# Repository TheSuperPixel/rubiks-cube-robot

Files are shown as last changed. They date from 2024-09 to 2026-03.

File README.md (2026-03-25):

# 三阶魔方还原机器人
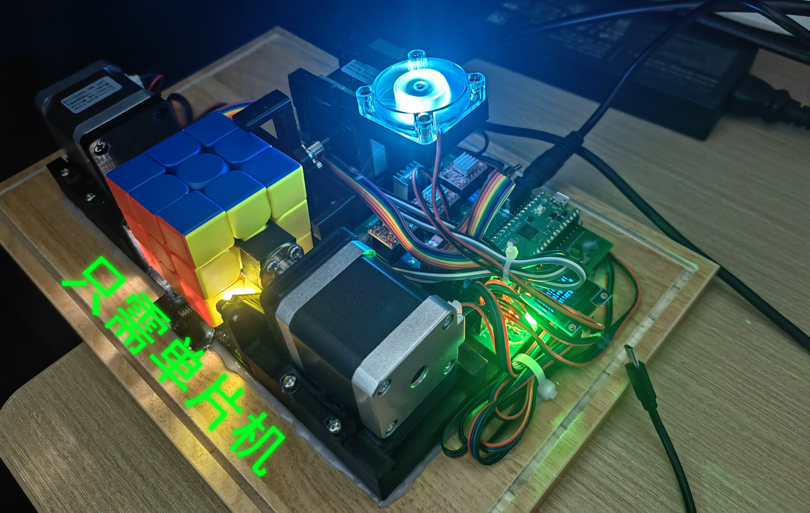
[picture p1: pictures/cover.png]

## 介绍
低成本魔方机器人设计，总物料成本200元左右。 含单片机源码（c语言）、结构图和PCB工程。 使用**树莓派pico单片机**控制，控制和魔方求解都使用单片机完成。 
工程的主要部分参照了B站“爱跑步的小何”的三阶魔方机器人开源工程，但是在这个工程的基础上，添加了江协科技的OLED驱动库，制作了用户菜单页面，使得机器人不仅能还原魔方，还能根据用户的选择，做出不同的魔方花样。
代码结构图是我在阅读原版开源项目时为了方便理解绘制的，仅供参考
## 关于硬件设计
使用嘉立创专业版打开pcb文件夹下的工程文件即可。主控选用树莓派pcio单片机，步进电机驱动模块接口连接A4988模块模块，其他元件参照电路板工程设计，焊接完成后，参照演示视频，设置拨码开关，三个电机的细分调节档位全部拨到1，颜色传感器灯开关全部拨到0，电机待机开关全部设置为无效。因为没有高速时序要求，PCB使用了自动布线，暂时不影响正常使用。

## 关于结构设计
使用**ABS材料**3D打印，尤其是夹魔方的结构件，对强度要求较高。

## 单片机固件编译(./src)
推荐使用**Linux**系统进行开发，可按照官方文档中的脚本搭建开发环境。不推荐Windows系统下搭建，坑很多的。

搭建好之后，修改**CMakeLists.txt**，把**PICO_SDK_PATH**设置为正确的路径
````
set(PICO_SDK_PATH "/home/your_name/pico2/pico-sdk")
#"your_name"need to change to your user name!
````
然后编译项目
````
cd src
mkdir build
cmake .
make -j2
````
然后找到cube_robot.uf2，刷写到单片机即可。

可以连接USB，使用minicom -D /dev/ttyACM0指令查看调试信息，例如：
````
color_detect: FLDFUUUDBDLRURRFDLBFRDFBFLRDDURDBBUBLURBLRLBLFFUFBLDRU
stage=0, D' B U' L F' 
stage=1, B2 R2 U2 F2 D R' L' U L' 
stage=2, R2 D' F2 D2 R2 D R2 D' B2 D' 
stage=3, B2 R2 U2 B2 U2 L2 U2 L2 F2 R2 B2 
````
## 参考资料
1.B站“爱跑步的小何”三阶魔方机器人工程 https://gitee.com/hemn1990/rubiks-cube-robot<br>
2.江协科技OLED驱动 https://www.bilibili.com/video/BV1EN41177Pc

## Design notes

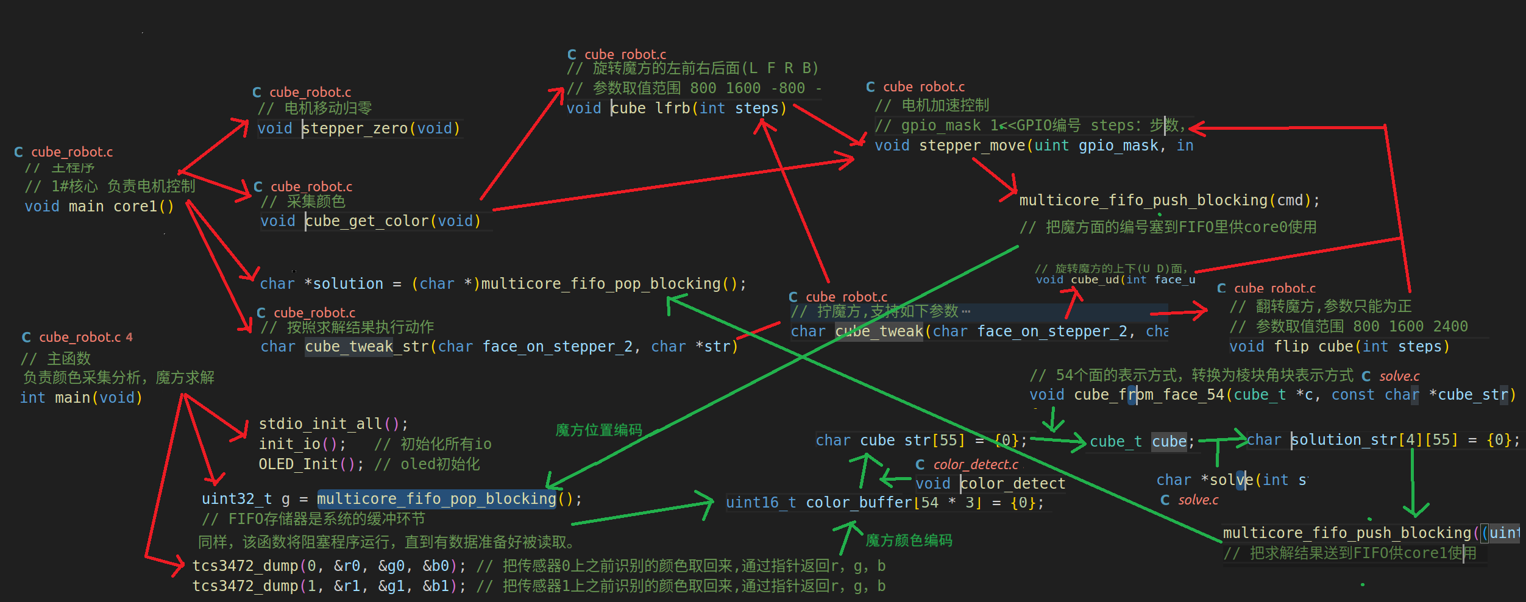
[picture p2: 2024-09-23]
代码结构.png

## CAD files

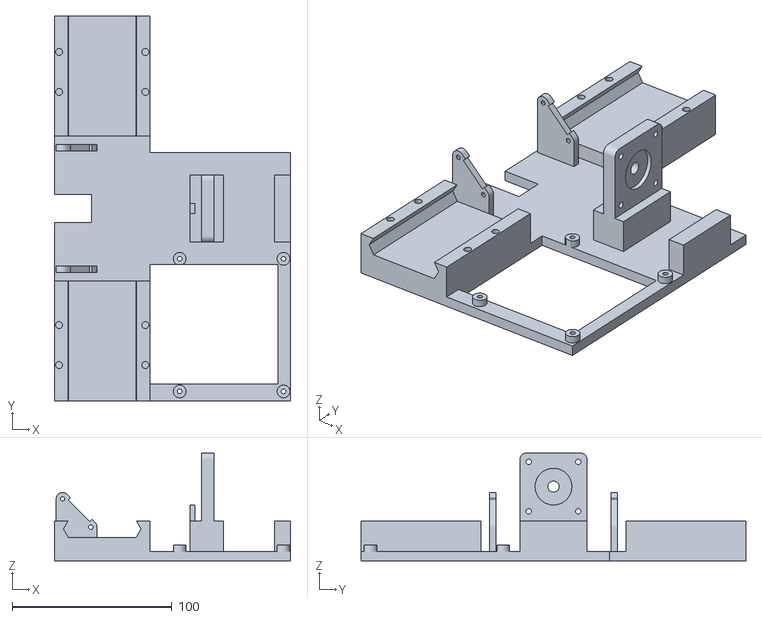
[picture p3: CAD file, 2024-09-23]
3D_print_STL/3d_print_main.stl
148.0 x 241.0 x 67.5

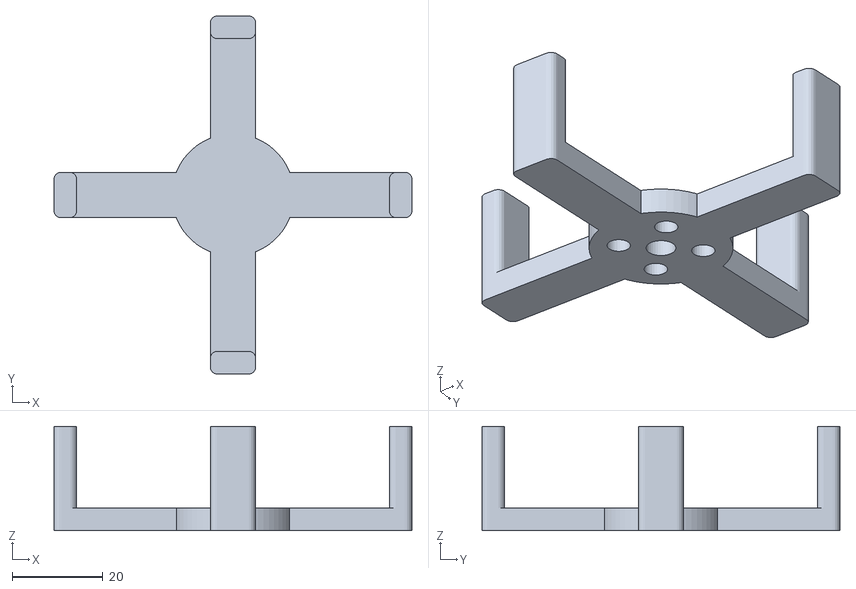
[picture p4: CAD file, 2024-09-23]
3D_print_STL/3d_print_cube_spin.stl
79.0 x 79.0 x 23.0

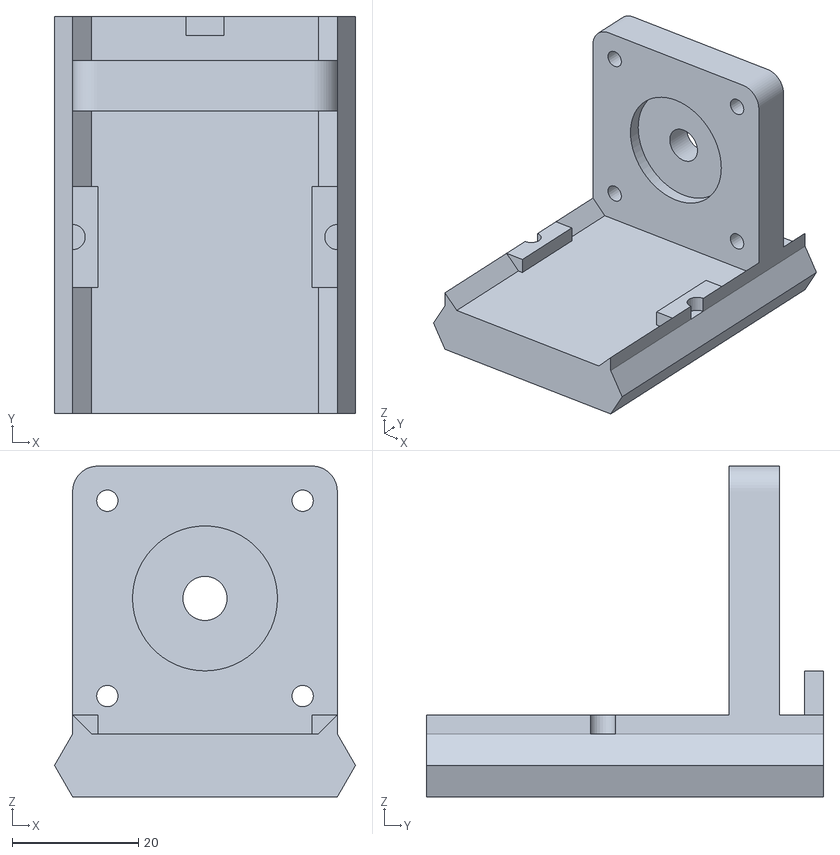
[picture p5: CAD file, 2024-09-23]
3D_print_STL/3d_print_stepper_shelf_x2.stl
47.8 x 63.0 x 52.5

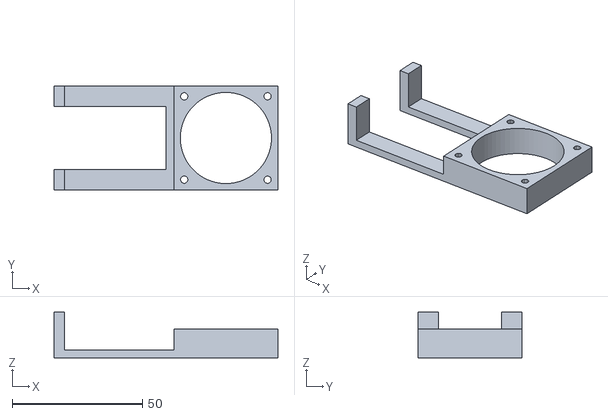
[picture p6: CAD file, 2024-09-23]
3D_print_STL/fan_holder.stl
86.0 x 40.0 x 17.5

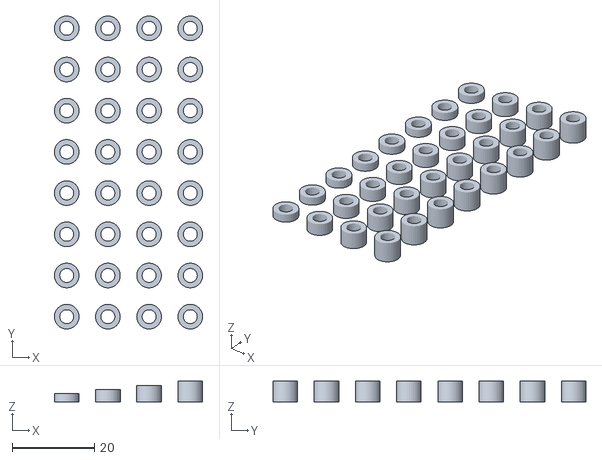
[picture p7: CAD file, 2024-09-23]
3D_print_STL/cylinder_reserve.stl
36.0 x 76.0 x 5.00

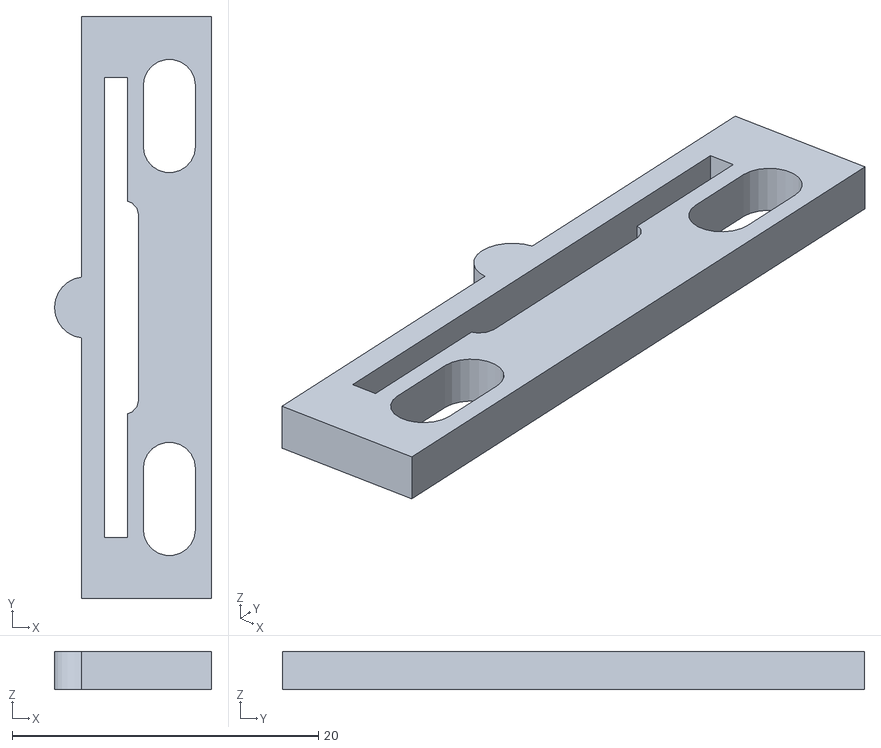
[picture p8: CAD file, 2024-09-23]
3D_print_STL/3d_print_spring_x4.stl
10.2 x 38.0 x 2.50

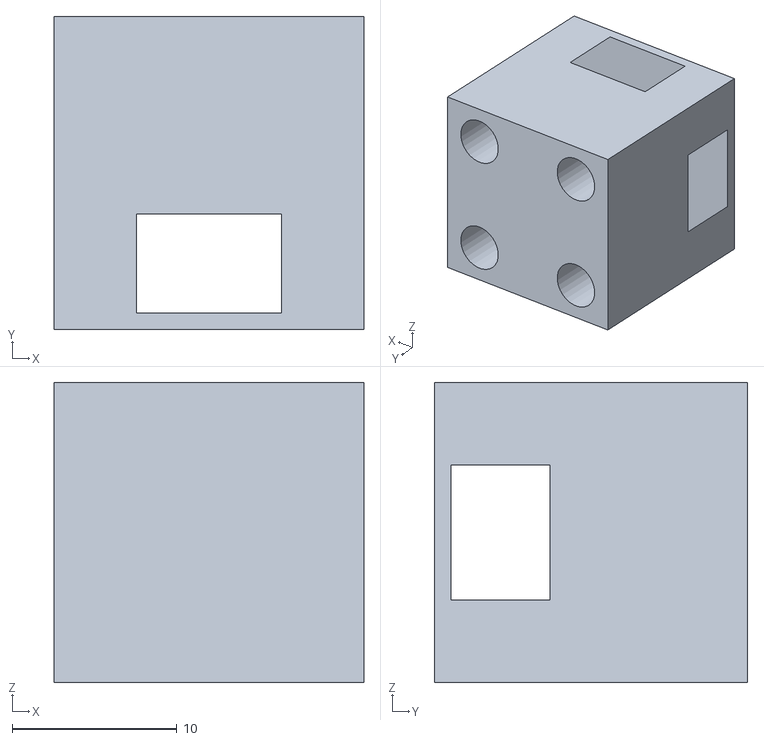
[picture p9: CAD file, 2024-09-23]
3D_print_STL/3d_print_claw_x2.stl
18.8 x 19.0 x 18.2

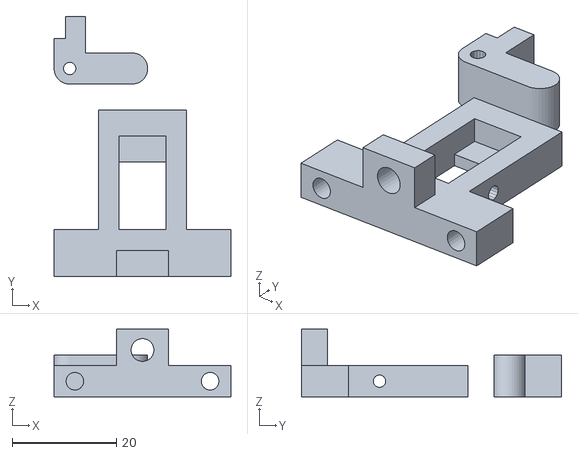
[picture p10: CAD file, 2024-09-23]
3D_print_STL/弹簧组件.stl
34.0 x 50.0 x 13.0

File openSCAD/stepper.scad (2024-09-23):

$fa=6;
$fs=0.5;



stepper42();
translate([0,0,23]) rotate([180,0,0]) flange();
module flange(){
    difference(){
        union(){
            cylinder(h=2,d=22);
            cylinder(h=12,d=10);
        }
        cylinder(h=99,d=5,center=true);
        translate([8,0,0]) cylinder(h=99,d=3,center=true);
        translate([-8,0,0]) cylinder(h=99,d=3,center=true);
        translate([0,-8,0]) cylinder(h=99,d=3,center=true);
        translate([0,8,0]) cylinder(h=99,d=3,center=true);
    }
}


module stepper42(){
    union(){
        top();
        translate([0,0,-8]) mid();
        translate([0,0,-8-9.5-23-8]) mirror([0,0,1]) bot();
    }
}


module mid(){
    mid_r = 8;
    offset_xy = 42/2 - mid_r;
    length = 23+8; // 硅钢片高度
    hull(){
        translate([offset_xy, offset_xy, -length]) cylinder(h=length, r=mid_r, $fn=4);
        translate([offset_xy, -offset_xy, -length]) cylinder(h=length, r=mid_r, $fn=4);
        translate([-offset_xy, offset_xy, -length]) cylinder(h=length, r=mid_r, $fn=4);
        translate([-offset_xy, -offset_xy, -length]) cylinder(h=length, r=mid_r, $fn=4);
    }
}
module top(){
    top_r = 4;
    offset_xy = 42/2 - top_r;
    length = 23+2; // 电机轴长度
    union(){
        difference(){
            hull(){
                translate([offset_xy, offset_xy, -8]) cylinder(h=8, r=top_r, $fn=4);
                translate([offset_xy, -offset_xy, -8]) cylinder(h=8, r=top_r, $fn=4);
                translate([-offset_xy, offset_xy, -8]) cylinder(h=8, r=top_r, $fn=4);
                translate([-offset_xy, -offset_xy, -8]) cylinder(h=8, r=top_r, $fn=4);
            }
            translate([31/2, 31/2, 0]) cylinder(h=20,d=2.5,center=true); 
            translate([-31/2, 31/2, 0]) cylinder(h=20,d=2.5,center=true);
            translate([31/2, -31/2, 0]) cylinder(h=20,d=2.5,center=true);
            translate([-31/2, -31/2, 0]) cylinder(h=20,d=2.5,center=true);       
        }
        difference(){
            cylinder(h=2,d=22);
            cylinder(h=20,d=9,center=true);
        }
        difference(){
             cylinder(h=length,d=5);
             translate([-5/2, 4.5/2, 0]) cube([5,5,length]);
        }
    }
}
module bot()
{
    bot_r = 4;
    offset_xy = 42/2 - bot_r;
    union(){
        difference(){
            hull(){
                translate([offset_xy, offset_xy, -9.5]) cylinder(h=9.5, r=bot_r, $fn=4);
                translate([offset_xy, -offset_xy, -9.5]) cylinder(h=9.5, r=bot_r, $fn=4);
                translate([-offset_xy, offset_xy, -9.5]) cylinder(h=9.5, r=bot_r, $fn=4);
                translate([-offset_xy, -offset_xy, -9.5]) cylinder(h=9.5, r=bot_r, $fn=4);
            }
            translate([31/2, 31/2, 0]) cylinder(h=20,d=3.5,center=true); 
            translate([-31/2, 31/2, 0]) cylinder(h=20,d=3.5,center=true);
            translate([31/2, -31/2, 0]) cylinder(h=20,d=3.5,center=true);
            translate([-31/2, -31/2, 0]) cylinder(h=20,d=3.5,center=true);
            translate([31/2, 31/2, -2.5]) cylinder(h=20,d=6); 
            translate([-31/2, 31/2, -2.5]) cylinder(h=20,d=6);
            translate([31/2, -31/2, -2.5]) cylinder(h=20,d=6);
            translate([-31/2, -31/2, -2.5]) cylinder(h=20,d=6);
            translate([0, 0, -3.5]) cylinder(h=20,d=9);
        }
        translate([-16/2,42/2,-9.5])cube([16,6,9.5]);
    }
}

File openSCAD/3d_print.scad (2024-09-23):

$fa=6;
$fs=0.5;
use <main.scad>



// 以下分别打印1个
//base_board();
//cube_spin();
rotate([180,0,0]) fan_holder();

// 以下分别打印2个
//claw_3d_print();
//stepper_shelf();

// 以下分别打印4个
//spring();


// 垫柱，打印不同尺寸的备用
/*
for(i=[0:7]){
    translate([10*0,i*10,0])cyl(2);
    translate([10*1,i*10,0])cyl(3);
    translate([10*2,i*10,0])cyl(4);
    translate([10*3,i*10,0])cyl(5);
}
*/

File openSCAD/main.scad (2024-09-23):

use <stepper.scad>
use <rubik_cube.scad>

//rotate([90,0,0]) stepper42();

$fa=6;
$fs=0.5;
// 滚花螺母孔径，需要比滚花螺母直径略小一点
m3_nut_hole_d = 4.4;
// m3螺丝孔，直接把螺丝拧到塑料件里
m3_hole_d = 2.8;
// 魔方旋转角度
cube_rotate=0; //0 78 45


// ------------------------------------------------------------------
//夹持魔方的结构，需要根据使用的魔方调整形状
//对强度要求较高，使用FDM原理的3D打印机，需要注意打印方向，4个孔面向X或者Y方向都行
//可以微调尺寸，解决3D打印ABS小尺寸零件时变形的问题
//根据打印机情况和使用的耗材类型调整（使用PLA的话不用调，基本不变形，但是强度很低）
//claw_3d_print();
claw_size_x=18.7+0.1;
claw_size_y=18.7-0.5;
claw_r=5;

module claw_3d_print()
{
    rotate([90,0,0]){
        // 固定魔方的爪子，打印2个
        claw();
        //支撑，打完割掉
        translate([-claw_size_x/2,-claw_size_y/2, 18]) cube([claw_size_x,claw_size_y,1]); 
    }
}

module claw(){
    difference(){
        union(){
            translate([-claw_size_x/2, -claw_size_y/2, 0 ]) cube([claw_size_x,claw_size_y,12]);
            translate([-claw_size_x/2, -claw_size_y/2, 12]) claw_1(0);
            translate([claw_size_x/2,  -claw_size_y/2, 12]) claw_1(1);
            translate([claw_size_x/2,  claw_size_y/2,  12]) claw_1(2);
            translate([-claw_size_x/2, claw_size_y/2,  12]) claw_1(3);
        }
        union(){
            for(i=[0:3]){
                rotate([0,0,45+90*i]) {
                    translate([8,0,0]) cylinder(h=7, d=m3_nut_hole_d);
                }
            }
        }
    }
}

module claw_1(dir)
{
    rotate([0,0,dir*90]){
        difference(){
            cube([claw_r, claw_r, 6]);
            translate([claw_r, claw_r, 0]) cylinder(h=6,r=claw_r);
        }
        //intersection() {
        //    cylinder(h=6, r=3.5, $fn=4);
        //    cube([3.5, 3.5, 6]);
        //}
    }
}

// ------------------------------------------------------------------
// 可活动步进电机支架 打印2个
module m3_hole(len1=10, len2=3)
{
    union(){
        translate([0,0,len2]) cylinder(h=len1, d=3.4);
        cylinder(h=len2, d=6);
    }
}

module stepper_shelf(style=0){
    union(){
        // 固定步进电机
        translate([0,0,42/2+0.5]) rotate([90,0,0]){
            difference(){
                hull(){
                    dst = 42/2-4;
                    translate([-dst,dst,0]) cylinder(h=8,r=4);
                    translate([dst,dst,0])  cylinder(h=8,r=4);
                    translate([-dst,-dst-0.5,4]) cube(8,center=true);
                    translate([dst,-dst-0.5,4])  cube(8,center=true);
                }
                translate([31/2, 31/2, 0])  m3_hole(10,3);
                translate([-31/2, 31/2, 0]) m3_hole(10,3);
                translate([31/2, -31/2, 0]) m3_hole(10,3);
                translate([-31/2, -31/2, 0])m3_hole(10,3);
                translate([0, 0, 8-2-0.5]) cylinder(h=10,d=22+1);
                cylinder(h=20,d=7,center=true);
            }
        }
        // 固定霍尔传感
        sensour_height = 10;
        translate([0,5.5,sensour_height/2]){
            cube([6,3,sensour_height],center=true);
        }
        
        if(style == 0){
            // 滑块
            size_x = 42;
            size_y = 48+15;
            height = 10;
            r1 = height/2/sin(60);
            difference(){
                union(){
                    translate([-size_x/2+r1/2,-size_y/2+7,-height/2]) rotate([90,0,0]) 
                        cylinder(size_y, r=r1, center=true, $fn=6);
                    translate([size_x/2-r1/2,-size_y/2+7,-height/2]) rotate([90,0,0]) 
                        cylinder(size_y, r=r1, center=true, $fn=6);
                    translate([0,-size_y/2+7,-height/2]) 
                        cube([size_x,size_y,10],center=true);
                }
            }
            // 
            for(i=[0,1]){
                mirror([i,0,0])
                    difference(){
                        union(){
                            translate([size_x/2,-size_y/2+7,0]) rotate([90,0,0]) 
                                cylinder(h=size_y,d=6,center=true, $fn=4);
                            translate([size_x/2-4/2,-28, 0])
                                cube([4,16,6],center=true);
                        }
                        translate([size_x/2,-28, 0])
                            cylinder(h=6,d=4);
                        translate([size_x/2+3,-size_y/2+7,0]) rotate([90,0,0]) 
                            cube([6,6,size_y+1],center=true);
                    }
            }
        }
        // 固定电机，不可活动
        if(style == 1){
            size_x = 42;
            size_y = 48+8+5;
            height = 20;
            translate([0,-(size_y-40)/2+7,-height/2])
                cube([size_x,size_y-40,height],center=true);
            translate([0,-51,-height/2])
                cube([size_x,10,height],center=true);
        }
    }
}
// ------------------------------------------------------------------
// 定位弹片，打印4个
module spring(){
    spring_height=2.5;
    translate([-5.5,0,0])
    difference(){
        cylinder(h=spring_height,d=4,center=true);
        translate([10,0,0]) cube([20,20,20],center=true);
    }
    difference(){
        translate([-1.5,0,0]) cube([8.5,38,spring_height],center=true);
        translate([-5+1.5,0,0]) cube([1.5,30,99],center=true);
        hull(){
            translate([0,-25/2+2,0]) cylinder(h=99, d=3.4,center=true);
            translate([0,-25/2-2,0]) cylinder(h=99, d=3.4,center=true);
        }
        hull(){
            translate([0,25/2+2,0]) cylinder(h=99, d=3.4,center=true);
            translate([0,25/2-2,0]) cylinder(h=99, d=3.4,center=true);
        }
        hull(){
            translate([-3,+6,0]) cylinder(h=99, d=2,center=true);
            translate([-3,-6,0]) cylinder(h=99, d=2,center=true);
        }
    }
}

// ------------------------------------------------------------------
// 用于旋转魔方的十字结构
// 对强度要求较高，适当提高填充和壁厚
module cube_spin()
{
    difference(){
        union(){
            translate([0,0,2.5]) cube([72,10,5],center=true);
            translate([0,0,2.5]) rotate([0,0,90]) cube([72,10,5],center=true);
            cylinder(h=5,d=27);
            for(i=[0:3]){
                rotate([0,0,90*i]) {
                    //translate([64/2+5,-5,0]) cube([5,10,23]);
                    hull(){
                       translate([38,5-1.5,0]) cylinder(h=23,r=1.5);
                       translate([38,-5+1.5,0]) cylinder(h=23,r=1.5);
                       translate([38-2,5-1.5,0]) cylinder(h=23,r=1.5);
                       translate([38-2,-5+1.5,0]) cylinder(h=23,r=1.5);
                    }
                }
            }
        }
        for(i=[0:3]){
            rotate([0,0,45+90*i]) {
                translate([8,0,-0.5]) cylinder(h=5, d=m3_nut_hole_d);
            }
        }
        translate([0,0,-0.5]) cylinder(h=5, d=5.6);
    }
}

// ------------------------------------------------------------------
// 使魔方中间层只能单向旋转的部件
module cube_block(){
    difference(){// 主体
        translate([0,1,0]) cube([17,32,6],center=true);
        translate([0,3,0]) cube([9,18,99],center=true);
        rotate([0,-90,0]) cylinder(h=99,d=2.4,center=true);
            
    }
    difference(){// 弹簧固定器
        translate([-5,-15,0]) cube([10,5,10]);
        translate([0,0,6]) rotate([90,0,0]) cylinder(h=99,d=m3_nut_hole_d);
    }
    translate([-5,7,-3]) cube([10,9,2]);// 底部限位
    difference(){// 固定螺丝孔
        translate([0,-10.5,0]) cube([34,9,6],center=true);
        translate([-13,30,00]) rotate([90,0,0]) cylinder(h=99,d=3.4);
        translate([13,30,0]) rotate([90,0,0]) cylinder(h=99,d=3.4);
    }
    
    //rotate([0,0,0]) //x =18
    translate([4,0,0]) rotate([0,-90,0]) difference(){
        union(){
            hull(){
                translate([18-6,0,0]) cylinder(h=8,d=6);
                cylinder(h=8,d=6);
            }
            hull(){
                translate([-3,5,0]) cube([6,5,8]);
                cylinder(h=8,d=6);
            }
        }
        translate([-3-0.2,6-0.2,0-0.2]) cube([2+0.4,5+0.4,8+0.4]);
        cylinder(h=99,d=2.4,center=true);
    }
}
// 滑轨
module rail(){
    dx=60;
    dy=75;
    height=10;
    height_bot=9;
    gap=0.4;//滑块间隙
    cut_d=42+2*5*tan(30)+gap*2;
    translate([0,-dy/2+12,-height/2]) {
        union(){
            difference(){
                translate([0,0,-height_bot/2])
                    cube([dx,dy,height+height_bot],center=true);
                rotate([90,0,0])
                    cylinder(h=99,d=cut_d,center=true,$fn=6);
                // 弹片固定孔
                translate([27,10,5-7]) cylinder(h=99, d=m3_nut_hole_d);
                translate([27,-15,5-7]) cylinder(h=99, d=m3_nut_hole_d);
                translate([-27,10,5-7]) cylinder(h=99, d=m3_nut_hole_d);
                translate([-27,-15,5-7]) cylinder(h=99, d=m3_nut_hole_d);
            }
            translate([0,0,-height/2-height_bot/2-gap/2])
                cube([dx,dy,height_bot-gap],center=true);
        }
    }
}
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

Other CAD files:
openSCAD/rubik_cube.scad

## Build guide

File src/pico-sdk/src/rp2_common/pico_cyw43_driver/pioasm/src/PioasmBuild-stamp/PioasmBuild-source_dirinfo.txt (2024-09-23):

# This is a generated file and its contents are an internal implementation detail.
# The download step will be re-executed if anything in this file changes.
# No other meaning or use of this file is supported.

method=source_dir
command=
source_dir=/home/wang/pico2/pico-sdk/tools/pioasm
work_dir=

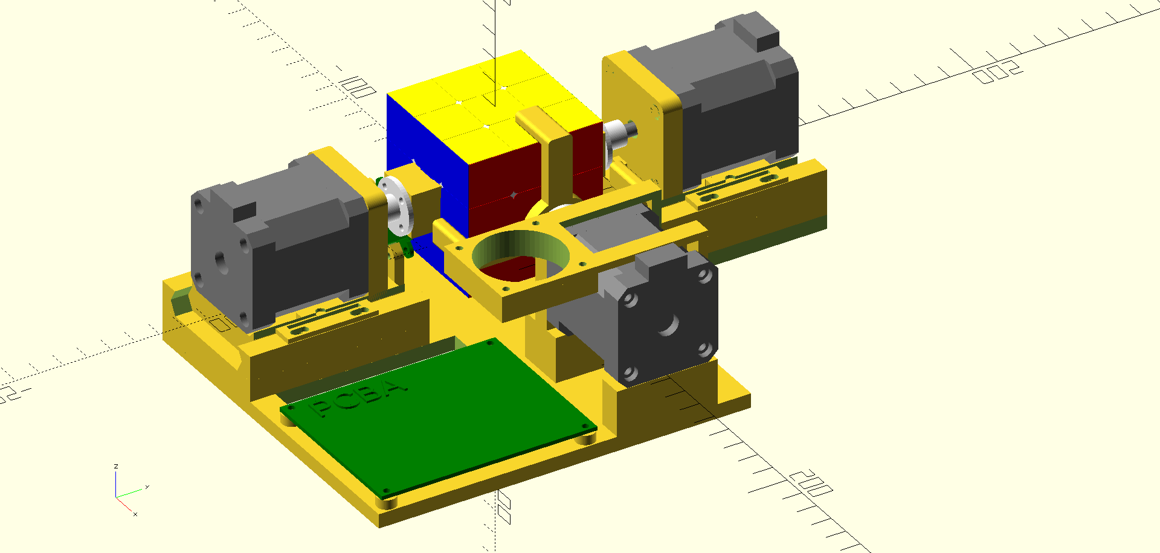
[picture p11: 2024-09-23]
装配图-带风扇架.png

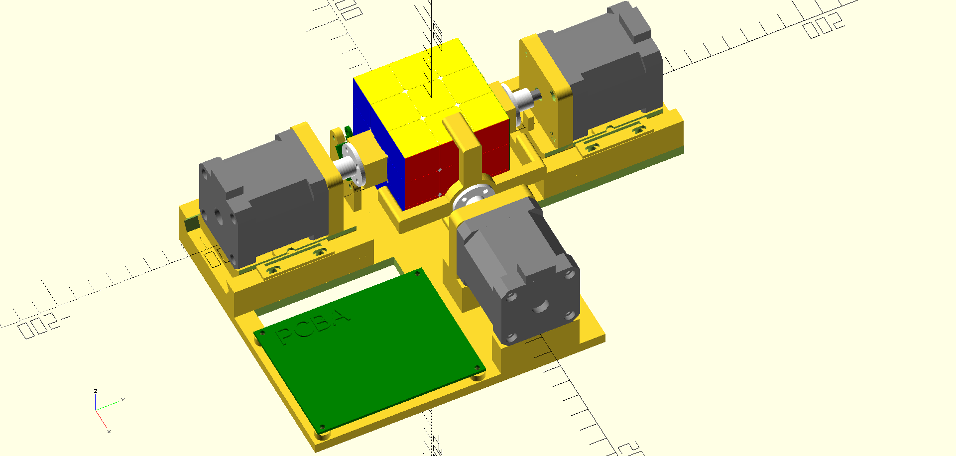
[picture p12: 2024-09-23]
装配图.png

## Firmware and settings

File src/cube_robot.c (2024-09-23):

#include <stdio.h>
#include <math.h>
#include "pico/stdlib.h"
#include "pico/multicore.h"
#include "color_detect.h"
// #include "hardware/i2c.h"
#include "solve.h"

#include "OLED.h"
// 步进电机使能信号 低有效 (20220706 由16改为2)
#define SPEPPER_EN 2
// 步进电机控制信号
#define SPEPPER_STEP0 11
#define SPEPPER_DIR0 10
#define SPEPPER_STEP1 9
#define SPEPPER_DIR1 8
#define SPEPPER_STEP2 7
#define SPEPPER_DIR2 6
// 霍尔开关，用于寻找零点
#define HALL_0 5
#define HALL_1 3
#define HALL_2 4
// 按键
#define BUTTON_0 0
#define BUTTON_1 1

#define BUTTON_FRONT 20
#define BUTTON_BACK 21
#define BUTTON_LEFT 18
#define BUTTON_RIGHT 19
#define BUTTON_PUSH 22

#define LED_RED 27
#define LED_GREEN 28
#define LED_BLUE 26

#define LED_PIN PICO_DEFAULT_LED_PIN

#define LED_PIN PICO_DEFAULT_LED_PIN
// 颜色传感器信号{{SDA,SCL},{SDA,SCL}}
const uint i2c_gpio[2][2] = {{14, 15}, {12, 13}};

// 根据实际测试结果调整电机初始角度
#define STEPPER0_OFFSET 485
#define STEPPER1_OFFSET 440
#define STEPPER2_OFFSET 325

// GPIO操作掩码，可以同时操作多个GPIO
#define MASK_STEPRR_01 ((1 << SPEPPER_STEP0) | (1 << SPEPPER_STEP1))
#define MASK_STEPRR_0 (1 << SPEPPER_STEP0)
#define MASK_STEPRR_1 (1 << SPEPPER_STEP1)
#define MASK_STEPRR_2 (1 << SPEPPER_STEP2)

// 顺时针、逆时针的定义，取决与驱动芯片的类型和电机的接线顺序
#define DIR0_CCW false
#define DIR0_CW true
#define DIR1_CCW false
#define DIR1_CW true
#define DIR2_CCW true
#define DIR2_CW false

#define RPM (200 * 16 / 60)
// #define SLOW_MODE
#ifdef SLOW_MODE
#define MAX_ACCEL 150000
#define V_START (30 * RPM)
#define V_MAX (90 * RPM)
#else
#define MAX_ACCEL 120000
#define V_START (150 * RPM)
#define V_MAX (300 * RPM)
#endif
// stepper_move(SPEPPER_STEP2,1600,180*RPM,300*RPM,200000);
// stepper_move(SPEPPER_STEP2,1600,180*RPM,300*RPM,150000);
int solve_color_flag = 0;

// 电机加速控制
// gpio_mask 1<<GPIO编号 steps：步数，v0：初始速度（脉冲/s），v：最高速度（脉冲/s），a：加速度（脉冲/s2）
void stepper_move(uint gpio_mask, int steps, float v0, float v, float a, const uint32_t *color_cmd)
{
    float vi = v0;
    const float F = 1000000.0f;                       // 定时器频率
    int s = (int)roundf((v * v - v0 * v0) / (2 * a)); // 计算加速过程需要的步数
    for (int i = 0; i < steps; i++)
    {
        // 计算需要的延时，单次计算过程耗时4us左右，debug和release模式差不多
        // 性能满足要求，不用考虑优化了
        //      4us
        //     +----+                      +----+
        //     |    |                      |    |
        //-----+    +----------------------+    +------
        //     |<----- roundf(F / vi) ----->
        absolute_time_t time_to_delay = get_absolute_time();
        gpio_set_mask(gpio_mask);
        float accel;
        if (i < s && i < steps / 2)
        {
            accel = a;
        }
        else if (i >= steps - s)
        {
            accel = -a;
        }
        else
        {
            accel = 0;
        }
        vi = sqrtf(vi * vi + 2.0f * accel);
        time_to_delay = delayed_by_us(time_to_delay, (uint64_t)roundf(F / vi));
        gpio_clr_mask(gpio_mask);
        // 旋转过程中采集颜色
        if (color_cmd && (i % 400) == 0)
        {
            uint32_t cmd = color_cmd[i / 400];
            if (cmd != 0)
            {
                multicore_fifo_push_blocking(cmd);
            }
        }
        sleep_until(time_to_delay);
    }
    if (color_cmd && (steps % 400) == 0)
    {
        uint32_t cmd = color_cmd[steps / 400];
        if (cmd != 0)
        {
            multicore_fifo_push_blocking(cmd); // 把魔方面的编号塞到FIFO里供core0使用
        }
    }
}
// 电机移动归零
void stepper_zero(void)
{
    bool s0, s1, s2;
    bool s0_ok = false;
    bool s1_ok = false;
    bool s2_ok = false;
    s0 = gpio_get(HALL_0);
    s1 = gpio_get(HALL_1);
    s2 = gpio_get(HALL_2);

    // 让三个电机一直转直到霍尔检测到
    while (!(s0_ok && s1_ok && s2_ok)) // s0_ok和s1_ok和s2_ok都为0时才循环
    {
        if (s0_ok == false)
        {
            gpio_put(SPEPPER_STEP0, 1);
            sleep_us(4);
            gpio_put(SPEPPER_STEP0, 0);
            if (!s0 && gpio_get(HALL_0))
                s0_ok = true;
            s0 = gpio_get(HALL_0);
        }
        if (s1_ok == false)
        {
            gpio_put(SPEPPER_STEP1, 1);
            sleep_us(4);
            gpio_put(SPEPPER_STEP1, 0);
            if (!s1 && gpio_get(HALL_1))
                s1_ok = true;
            s1 = gpio_get(HALL_1);
        }
        if (s2_ok == false)
        {
            gpio_put(SPEPPER_STEP2, 1);
            sleep_us(4);
            gpio_put(SPEPPER_STEP2, 0);
            if (!s2 && gpio_get(HALL_2))
                s2_ok = true;
            s2 = gpio_get(HALL_2);
        }
        sleep_us(400);
    }

    // 三个电机都转到初始位置
    stepper_move(MASK_STEPRR_0, STEPPER0_OFFSET, 100 * RPM, 300 * RPM, 150000, 0);
    stepper_move(MASK_STEPRR_1, STEPPER1_OFFSET, 100 * RPM, 300 * RPM, 150000, 0);
    stepper_move(MASK_STEPRR_2, STEPPER2_OFFSET, 100 * RPM, 300 * RPM, 150000, 0);
}
// IO初始化
void init_io(void)
{
    // 初始化引脚
    gpio_init(LED_PIN);
    gpio_init(SPEPPER_EN);
    gpio_init(SPEPPER_DIR0);
    gpio_init(SPEPPER_DIR1);
    gpio_init(SPEPPER_DIR2);
    gpio_init(SPEPPER_STEP0);
    gpio_init(SPEPPER_STEP1);
    gpio_init(SPEPPER_STEP2);
    gpio_init(SPEPPER_STEP2);
    gpio_init(HALL_0);
    gpio_init(HALL_1);
    gpio_init(HALL_2);
    gpio_init(BUTTON_0);
    gpio_init(BUTTON_1);

    gpio_init(BUTTON_LEFT);
    gpio_init(BUTTON_RIGHT);
    gpio_init(BUTTON_FRONT);
    gpio_init(BUTTON_BACK);
    gpio_init(BUTTON_PUSH);

    gpio_init(LED_RED);
    gpio_init(LED_GREEN);
    gpio_init(LED_BLUE);

    // 设置为低电平
    gpio_put(SPEPPER_EN, 0);
    gpio_put(SPEPPER_DIR0, 0);
    gpio_put(SPEPPER_DIR1, 0);
    gpio_put(SPEPPER_DIR2, 0);
    gpio_put(SPEPPER_STEP0, 0);
    gpio_put(SPEPPER_STEP1, 0);
    gpio_put(SPEPPER_STEP2, 0);

    gpio_put(LED_RED, 0);
    gpio_put(LED_GREEN, 0);
    gpio_put(LED_BLUE, 0);
    // 设置引脚方向
    gpio_set_dir(LED_PIN, GPIO_OUT);
    gpio_set_dir(SPEPPER_EN, GPIO_OUT);
    gpio_set_dir(SPEPPER_DIR0, GPIO_OUT);
    gpio_set_dir(SPEPPER_DIR1, GPIO_OUT);
    gpio_set_dir(SPEPPER_DIR2, GPIO_OUT);
    gpio_set_dir(SPEPPER_STEP0, GPIO_OUT);
    gpio_set_dir(SPEPPER_STEP1, GPIO_OUT);
    gpio_set_dir(SPEPPER_STEP2, GPIO_OUT);

    gpio_set_dir(HALL_0, GPIO_IN);
    gpio_set_dir(HALL_1, GPIO_IN);
    gpio_set_dir(HALL_2, GPIO_IN);
    gpio_set_dir(BUTTON_0, GPIO_IN);
    gpio_set_dir(BUTTON_1, GPIO_IN);

    gpio_set_dir(BUTTON_LEFT, GPIO_IN);
    gpio_set_dir(BUTTON_RIGHT, GPIO_IN);
    gpio_set_dir(BUTTON_FRONT, GPIO_IN);
    gpio_set_dir(BUTTON_BACK, GPIO_IN);
    gpio_set_dir(BUTTON_PUSH, GPIO_IN);
    gpio_set_dir(LED_RED, GPIO_OUT);
    gpio_set_dir(LED_GREEN, GPIO_OUT);
    gpio_set_dir(LED_BLUE, GPIO_OUT);
    // 设置上拉输入
    gpio_pull_up(HALL_0);
    gpio_pull_up(HALL_1);
    gpio_pull_up(HALL_2);
    gpio_pull_up(BUTTON_0);
    gpio_pull_up(BUTTON_1);

    gpio_pull_up(BUTTON_LEFT);
    gpio_pull_up(BUTTON_RIGHT);
    gpio_pull_up(BUTTON_FRONT);
    gpio_pull_up(BUTTON_BACK);
    gpio_pull_up(BUTTON_PUSH);
    /*
        gpio_set_function(12, GPIO_FUNC_I2C);
        gpio_set_function(13, GPIO_FUNC_I2C);
        gpio_set_function(14, GPIO_FUNC_I2C);
        gpio_set_function(15, GPIO_FUNC_I2C);
        i2c_init(i2c0, 20000);
        i2c_init(i2c1, 20000);
    */
    // 初始化iic引脚
    for (int i = 0; i < 2; i++)
    {
        for (int j = 0; j < 2; j++)
        {
            gpio_init(i2c_gpio[i][j]);
            gpio_pull_up(i2c_gpio[i][j]);
            gpio_set_dir(i2c_gpio[i][j], GPIO_IN);
            gpio_put(i2c_gpio[i][j], 0);
        }
    }
}
void LED_Set(int led_color)
{
    if (led_color == 0)
    {
        gpio_put(LED_RED, 0);
        gpio_put(LED_GREEN, 0);
        gpio_put(LED_BLUE, 0);
    }
    if (led_color == 1)
    {
        gpio_put(LED_RED, 1);
        gpio_put(LED_GREEN, 0);
        gpio_put(LED_BLUE, 0);
    }
    if (led_color == 2)
    {
        gpio_put(LED_RED, 0);
        gpio_put(LED_GREEN, 1);
        gpio_put(LED_BLUE, 0);
    }
    if (led_color == 3)
    {
        gpio_put(LED_RED, 0);
        gpio_put(LED_GREEN, 0);
        gpio_put(LED_BLUE, 1);
    }
    if (led_color == 4)
    {
        gpio_put(LED_RED, 1);
        gpio_put(LED_GREEN, 1);
        gpio_put(LED_BLUE, 0);
    }
    if (led_color == 5)
    {
        gpio_put(LED_RED, 1);
        gpio_put(LED_GREEN, 0);
        gpio_put(LED_BLUE, 1);
    }
    if (led_color == 6)
    {
        gpio_put(LED_RED, 0);
        gpio_put(LED_GREEN, 1);
        gpio_put(LED_BLUE, 1);
    }
    if (led_color == 7)
    {
        gpio_put(LED_RED, 1);
        gpio_put(LED_GREEN, 1);
        gpio_put(LED_BLUE, 1);
    }
}
// --------------- 魔方控制部分 -----------------------
// 旋转魔方的上下(U D)面，注意参数只支持正数，U为逆时针，D为顺时针
// 参数取值范围0 800 1600 2400
void cube_ud(int face_u, int face_d)
{
    const int gap = 24;
    // 步骤1：卡住魔方中间层
    gpio_put(SPEPPER_DIR0, DIR0_CCW);
    gpio_put(SPEPPER_DIR1, DIR1_CW);
    stepper_move(MASK_STEPRR_01, gap, V_START, V_MAX, MAX_ACCEL, 0);
    // 步骤2：旋转需要的角度
    int min_val = face_u < face_d ? face_u : face_d;
    if (min_val >= 0)
        stepper_move(MASK_STEPRR_01, min_val, V_START, V_MAX, MAX_ACCEL, 0);
    face_u -= min_val;
    face_d -= min_val;
    if (face_u >= 0)
        stepper_move(MASK_STEPRR_0, face_u, V_START, V_MAX, MAX_ACCEL, 0);
    if (face_d >= 0)
        stepper_move(MASK_STEPRR_1, face_d, V_START, V_MAX, MAX_ACCEL, 0);
    // 步骤3：恢复初始位置
    gpio_put(SPEPPER_DIR0, DIR0_CW);
    gpio_put(SPEPPER_DIR1, DIR1_CCW);
    stepper_move(MASK_STEPRR_01, gap, V_START, V_MAX, MAX_ACCEL, 0);
}
// 旋转魔方的左前右后面(L F R B),参数正负都可以，正数表示顺时针，负数表示逆时针
// 参数取值范围 800 1600 -800 -1600
void cube_lfrb(int steps)
{
    bool dir;
    if (steps > 0)
    {
        dir = DIR2_CW;
    }
    else
    {
        dir = DIR2_CCW;
        steps = -steps;
    }
    // 步骤1：旋转臂接触魔方，接触之前应当减速，否则接触后受力突变，会丢步
    gpio_put(SPEPPER_DIR2, dir);
    stepper_move(MASK_STEPRR_2, 256, V_START, V_MAX, MAX_ACCEL, 0);
    // 步骤2：旋转需要的角度
    stepper_move(MASK_STEPRR_2, steps - 64, V_START, V_MAX, MAX_ACCEL, 0);
    // 步骤3：最后一小段要低速运转
    stepper_move(MASK_STEPRR_2, 64, V_START / 2, V_START / 2, MAX_ACCEL, 0);
    // 步骤4：恢复初始位置
    gpio_put(SPEPPER_DIR2, !dir);
    stepper_move(MASK_STEPRR_2, 256, V_START, V_MAX, MAX_ACCEL, 0);
}

// 翻转魔方,参数只能为正
// 参数取值范围 800 1600 2400
void flip_cube(int steps)
{
    gpio_put(SPEPPER_DIR0, DIR0_CW);
    gpio_put(SPEPPER_DIR1, DIR1_CCW);
    stepper_move(MASK_STEPRR_01, steps, V_START, V_MAX, MAX_ACCEL, 0);
}
// 采集颜色
void cube_get_color(void)
{
#define UD(x, y) (((x) << 8) | (y)) // 8位的x左移8位后和y拼合
    const uint32_t color_cmd_0_270_L[7] = {UD(36, 42), UD(23, 48), UD(38, 44), UD(10, 43), UD(9, 15), UD(50, 21), UD(11, 17)};
    const uint32_t color_cmd_1_180_R[5] = {0, UD(37, 16), UD(33, 27), UD(19, 52), UD(0, 6)};
    const uint32_t color_cmd_2_270_F[7] = {0, 0, UD(29, 35), UD(46, 25), UD(8, 2), 0, 0};
    const uint32_t color_cmd_3_180_B[5] = {0, 0, UD(18, 51), UD(12, 41), UD(47, 26)};
    const uint32_t color_cmd_4_270_R[7] = {0, 0, UD(45, 24), UD(39, 14), UD(20, 53), 0, 0};
    const uint32_t color_cmd_5_180_L[5] = {0, 0, 0, UD(5, 32), 0};
    // const uint32_t color_cmd_6_90_F[3]= {0,0,0};
    const uint32_t color_cmd_7_180_B[5] = {0, UD(3, 30), 0, UD(7, 28), 0};
    const uint32_t color_cmd_8_180[5] = {0, 0, 0, UD(1, 34), 0};

    gpio_put(SPEPPER_DIR0, DIR0_CW);
    gpio_put(SPEPPER_DIR1, DIR1_CCW);
    stepper_move(MASK_STEPRR_01, 2400, V_START, V_MAX, MAX_ACCEL, color_cmd_0_270_L);
    cube_lfrb(800);
    stepper_move(MASK_STEPRR_01, 1600, V_START, V_MAX, MAX_ACCEL, color_cmd_1_180_R);
    cube_lfrb(800);
    stepper_move(MASK_STEPRR_01, 2400, V_START, V_MAX, MAX_ACCEL, color_cmd_2_270_F);
    cube_lfrb(800);
    stepper_move(MASK_STEPRR_01, 1600, V_START, V_MAX, MAX_ACCEL, color_cmd_3_180_B);
    cube_lfrb(800);
    stepper_move(MASK_STEPRR_01, 2400, V_START, V_MAX, MAX_ACCEL, color_cmd_4_270_R);
    cube_lfrb(800);
    stepper_move(MASK_STEPRR_01, 1600, V_START, V_MAX, MAX_ACCEL, color_cmd_5_180_L);
    cube_lfrb(800);
    stepper_move(MASK_STEPRR_01, 800, V_START, V_MAX, MAX_ACCEL, 0);
    cube_lfrb(800);
    stepper_move(MASK_STEPRR_01, 1600, V_START, V_MAX, MAX_ACCEL, color_cmd_7_180_B);
    cube_lfrb(800);
    stepper_move(MASK_STEPRR_01, 1600, V_START, V_MAX, MAX_ACCEL, color_cmd_8_180);
}
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
int main(void)
{
    // sleep_ms(5000);
    stdio_init_all();
    init_io();   // 初始化所有io
    OLED_Init(); // oled初始化

    multicore_launch_core1(main_core1); // 启动core 1 核心

    // 检查颜色传感器是否正常，并且初始化
    for (int i = 0; i < 2; i++)
    {
        if (tcs3472_check_id(i))
        {
            tcs3472_enable(i);
            printf("tcs3472_check_id(%d) pass\n", i);
            OLED_Printf(0, i * 8, OLED_6X8, "color_id(%d) pass\n", i);
        }
        else
        {
            printf("tcs3472_check_id(%d) fail\n", i);
            OLED_Printf(0, 0, OLED_6X8, "color_id(%d) fail\n", i);
            while (1)
                ;
        }
        sleep_ms(100);
    }
    OLED_Printf(0, 16, OLED_6X8, "start stepper zero");
    OLED_Update();
    sleep_ms(1000);
    LED_Set(1);
    //  显示菜单
    int menu_1 = 0; // 菜单1高亮标记
    int menu_2 = 0; // 菜单2高亮标记
    int page = 0;   // 页数标记
    while (1)
    {
        if (gpio_get(BUTTON_FRONT) == 0)
        {
            sleep_ms(10);
            while (gpio_get(BUTTON_FRONT) == 0)
                ;
            sleep_ms(10);
            if (page == 0)
            {
                if (menu_1 == 1)
                {
                    menu_1 = 0;
                }
            }
            else if (page == 1)
            {
                if (menu_2 > 0)
                {
                    menu_2--;
                }
            }
        }
        if (gpio_get(BUTTON_BACK) == 0)
        {
            sleep_ms(10);
            while (gpio_get(BUTTON_BACK) == 0)
                ;
            sleep_ms(10);
            if (page == 0)
            {
                if (menu_1 == 0)
                {
                    menu_1 = 1;
                }
            }
            else if (page == 1)
            {
                if (menu_2 < 2)
                {
                    menu_2++;
                }
            }
        }
        if (gpio_get(BUTTON_LEFT) == 0)
        {
            sleep_ms(10);
            while (gpio_get(BUTTON_LEFT) == 0)
                ;
            sleep_ms(10);
            if (page == 1)
            {
                page = 0;
            }
        }
        if (page == 0)
        {
            OLED_Clear();
            OLED_Printf(0, 0, OLED_8X16, "function list");
            OLED_Printf(0, 16, OLED_8X16, "1: solve!");
            OLED_Printf(0, 32, OLED_8X16, "2: pattern");
            if (menu_1 == 0)
            {
                OLED_ShowChar(100, 16, '*', OLED_8X16);
                OLED_ShowChar(100, 32, ' ', OLED_8X16);
            }
            if (menu_1 == 1)
            {
                OLED_ShowChar(100, 16, ' ', OLED_8X16);
                OLED_ShowChar(100, 32, '*', OLED_8X16);
            }
            OLED_Update();
        }
        else if (page == 1)
        {
            OLED_Clear();
            OLED_Printf(0, 0, OLED_8X16, "pattern list");
            OLED_Printf(0, 16, OLED_8X16, "1: pattern1");
            OLED_Printf(0, 32, OLED_8X16, "2: pattern2");
            OLED_Printf(0, 48, OLED_8X16, "3: pattern3");
            if (menu_2 == 0)
            {
                OLED_ShowChar(100, 16, '*', OLED_8X16);
                OLED_ShowChar(100, 32, ' ', OLED_8X16);
                OLED_ShowChar(100, 48, ' ', OLED_8X16);
            }
            if (menu_2 == 1)
            {
                OLED_ShowChar(100, 16, ' ', OLED_8X16);
                OLED_ShowChar(100, 32, '*', OLED_8X16);
                OLED_ShowChar(100, 48, ' ', OLED_8X16);
            }
            if (menu_2 == 2)
            {
                OLED_ShowChar(100, 16, ' ', OLED_8X16);
                OLED_ShowChar(100, 32, ' ', OLED_8X16);
                OLED_ShowChar(100, 48, '*', OLED_8X16);
            }
            OLED_Update();
        }

        if (gpio_get(BUTTON_RIGHT) == 0)
        {
            sleep_ms(10);
            while (gpio_get(BUTTON_RIGHT) == 0)
                ;
            sleep_ms(10);
            if (page == 0)
            {
                if (menu_1 == 0)
                {
                    solve_color_flag = 1;
                    // OLED_Clear();
                    // OLED_Update();
                    break;
                }
                if (menu_1 == 1)
                {
                    page = 1;
                }
            }
            else if (page == 1)
            {
                if (menu_2 == 0)
                {
                    LED_Set(2);
                    char my_solution[40] = {
                        'F', '0', '0',
                        'F', '\'', '0',
                        'B', '0', '0',
                        'B', '\'', '0',
                        'L', '0', '0',
                        'L', '\'', '0',
                        'R', '0', '0',
                        'R', '\'', '0',
                        'U', '0', '0',
                        'U', '\'', '0',
                        'D', '0', '0',
                        'D', '\'', '0'};
                    cube_tweak_str('F', my_solution);
                    LED_Set(3);
                }
                else if (menu_2 == 1)
                {
                    LED_Set(2);
                    char my_solution[40] = {
                        'F', '0', '0',
                        'F', '0', '0',
                        'B', '0', '0',
                        'B', '0', '0',
                        'L', '0', '0',
                        'L', '0', '0',
                        'R', '0', '0',
                        'R', '0', '0',
                        'U', '0', '0',
                        'U', '0', '0',
                        'D', '0', '0',
                        'D', '0', '0'};
                    cube_tweak_str('F', my_solution);
                    LED_Set(3);
                }
                else if (menu_2 == 2) // F D2 L2 B D B' F2 U' F U F2 U2 F' L D F' U
                {
                    LED_Set(2);
                    char my_solution[75] = {
                        'F', '0', '0',
                        'D', '0', '0',
                        'D', '0', '0',
                        'L', '0', '0',
                        'L', '0', '0',
                        'B', '0', '0',
                        'D', '0', '0',
                        'B', '\'', '0',
                        'F', '0', '0',
                        'F', '0', '0',
                        'U', '\'', '0',
                        'F', '0', '0',
                        'U', '0', '0',
                        'F', '0', '0',
                        'F', '0', '0',
                        'U', '0', '0',
                        'U', '0', '0',
                        'F', '\'', '0',
                        'L', '0', '0',
                        'D', '0', '0',
                        'F', '\'', '0',
                        'U', '0', '0'};
                    cube_tweak_str('F', my_solution);
                    LED_Set(3);
                }
            }
        }
        solve_color_flag = 0;
    }

    // 还原魔方部分
    while (1)
    {
        // 在接到core1的通知时采集颜色
        for (int i = 0; i < 24; i++)
        {
            uint32_t g = multicore_fifo_pop_blocking();
            // FIFO存储器是系统的缓冲环节
            // 这个函数从FIFO中“弹出”数据。数据以int32格式返回。 同样，该函数将阻塞程序运行，直到有数据准备好被读取。
            if (g < 0xFFFF)
            {
                uint16_t r0, g0, b0, r1, g1, b1;
                tcs3472_dump(0, &r0, &g0, &b0); // 把传感器0上之前识别的颜色取回来,通过指针返回r，g，b
                tcs3472_dump(1, &r1, &g1, &b1); // 把传感器1上之前识别的颜色取回来,通过指针返回r，g，b
                color_buffer[(g >> 8) * 3 + 0] = r0;
                color_buffer[(g >> 8) * 3 + 1] = g0;
                color_buffer[(g >> 8) * 3 + 2] = b0;
                color_buffer[(g & 0xff) * 3 + 0] = r1;
                color_buffer[(g & 0xff) * 3 + 1] = g1;
                color_buffer[(g & 0xff) * 3 + 2] = b1;
                // printf("ID=(%u,%u) r0=%u g0=%u b0=%u r1=%u g1=%u b1=%u\n",g>>8,g&0xFF,r0,g0,b0,r1,g1,b1);
            }
        }
        // 识别颜色
        printf("color_buffer: %s\n", color_buffer);
        color_detect(color_buffer, cube_str); // 把color_buffer的rgb值转换为颜色的编号，存到cube_str
        for (int i = 0; i < 54 * 3; i++)
        {
            // 用完清理数据，这很重要，这BUG调了一小时
            // 魔方中间块对应的6个数据，每次重新采样是不会更新的
            color_buffer[i] = 0;
        }
        printf("color_detect: %s\n", cube_str);

        // OLED_Printf(0, 0, OLED_6X8, "get color ok!");
        // OLED_Printf(0, 8, OLED_6X8, "start solveing!");
        // OLED_Update();

        if (cube_str[0] != 0)
        {
            // 求解魔方
            cube_t cube;
            cube_from_face_54(&cube, cube_str); // 54个面的表示方式，转换为棱块角块表示方式
            for (int stage = 0; stage < 4; stage++)
            {
                char *p = solution_str[stage];
                p = solve(stage, &cube, p); // 求解魔方
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

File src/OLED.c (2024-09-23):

/***************************************************************************************
 * 本程序由江协科技创建并免费开源共享
 * 你可以任意查看、使用和修改，并应用到自己的项目之中
 * 程序版权归江协科技所有，任何人或组织不得将其据为己有
 *
 * 程序名称：				0.96寸OLED显示屏驱动程序（4针脚I2C接口）
 * 程序创建时间：			2023.10.24
 * 当前程序版本：			V1.1
 * 当前版本发布时间：		2023.12.8
 *
 * 江协科技官方网站：		jiangxiekeji.com
 * 江协科技官方淘宝店：	jiangxiekeji.taobao.com
 * 程序介绍及更新动态：	jiangxiekeji.com/tutorial/oled.html
 *
 * 如果你发现程序中的漏洞或者笔误，可通过邮件向我们反馈：feedback@jiangxiekeji.com
 * 发送邮件之前，你可以先到更新动态页面查看最新程序，如果此问题已经修改，则无需再发邮件
 ***************************************************************************************
 */

#include "OLED.h"
#include <string.h>
#include <math.h>
#include <stdio.h>
#include <stdarg.h>
#include "pico/stdlib.h"

// OLED
#define OLED_SCL_PIN 16
#define OLED_SDA_PIN 17

/**
 * 数据存储格式：
 * 纵向8点，高位在下，先从左到右，再从上到下
 * 每一个Bit对应一个像素点
 *
 *      B0 B0                  B0 B0
 *      B1 B1                  B1 B1
 *      B2 B2                  B2 B2
 *      B3 B3  ------------->  B3 B3 --
 *      B4 B4                  B4 B4  |
 *      B5 B5                  B5 B5  |
 *      B6 B6                  B6 B6  |
 *      B7 B7                  B7 B7  |
 *                                    |
 *  -----------------------------------
 *  |
 *  |   B0 B0                  B0 B0
 *  |   B1 B1                  B1 B1
 *  |   B2 B2                  B2 B2
 *  --> B3 B3  ------------->  B3 B3
 *      B4 B4                  B4 B4
 *      B5 B5                  B5 B5
 *      B6 B6                  B6 B6
 *      B7 B7                  B7 B7
 *
 * 坐标轴定义：
 * 左上角为(0, 0)点
 * 横向向右为X轴，取值范围：0~127
 * 纵向向下为Y轴，取值范围：0~63
 *
 *       0             X轴           127
 *      .------------------------------->
 *    0 |
 *      |
 *      |
 *      |
 *  Y轴 |
 *      |
 *      |
 *      |
 *   63 |
 *      v
 *
 */

/*全局变量*********************/

/**
 * OLED显存数组
 * 所有的显示函数，都只是对此显存数组进行读写
 * 随后调用OLED_Update函数或OLED_UpdateArea函数
 * 才会将显存数组的数据发送到OLED硬件，进行显示
 */
uint8_t OLED_DisplayBuf[8][128];

/*********************全局变量*/

/*引脚配置*********************/

/**
 * 函    数：OLED写SCL高低电平
 * 参    数：要写入SCL的电平值，范围：0/1
 * 返 回 值：无
 * 说    明：当上层函数需要写SCL时，此函数会被调用
 *           用户需要根据参数传入的值，将SCL置为高电平或者低电平
 *           当参数传入0时，置SCL为低电平，当参数传入1时，置SCL为高电平
 */
void OLED_W_SCL(uint8_t BitValue)
{
	/*根据BitValue的值，将SCL置高电平或者低电平*/
	gpio_put(OLED_SCL_PIN, BitValue);

	/*如果单片机速度过快，可在此添加适量延时，以避免超出I2C通信的最大速度*/
	//...
	sleep_us(1);
}

/**
 * 函    数：OLED写SDA高低电平
 * 参    数：要写入SDA的电平值，范围：0/1
 * 返 回 值：无
 * 说    明：当上层函数需要写SDA时，此函数会被调用
 *           用户需要根据参数传入的值，将SDA置为高电平或者低电平
 *           当参数传入0时，置SDA为低电平，当参数传入1时，置SDA为高电平
 */
void OLED_W_SDA(uint8_t BitValue)
{
	/*根据BitValue的值，将SDA置高电平或者低电平*/
	gpio_put(OLED_SDA_PIN, BitValue);

	/*如果单片机速度过快，可在此添加适量延时，以避免超出I2C通信的最大速度*/
	//...
	sleep_us(1);
}

/**
 * 函    数：OLED引脚初始化
 * 参    数：无
 * 返 回 值：无
 * 说    明：当上层函数需要初始化时，此函数会被调用
 *           用户需要将SCL和SDA引脚初始化为开漏模式，并释放引脚
 */
void OLED_GPIO_Init(void)
{
	uint32_t i, j;

	/*在初始化前，加入适量延时，待OLED供电稳定*/
	for (i = 0; i < 1000; i++)
	{
		for (j = 0; j < 1000; j++)
			;
	}
	gpio_init(OLED_SCL_PIN);
	gpio_init(OLED_SDA_PIN);
	gpio_set_dir(OLED_SCL_PIN, GPIO_OUT);
	gpio_set_dir(OLED_SDA_PIN, GPIO_OUT);

	/*释放SCL和SDA*/
	OLED_W_SCL(1);
	OLED_W_SDA(1);
}

/*********************引脚配置*/

/*通信协议*********************/

/**
 * 函    数：I2C起始
 * 参    数：无
 * 返 回 值：无
 */
void OLED_I2C_Start(void)
{
	OLED_W_SDA(1); // 释放SDA，确保SDA为高电平
	OLED_W_SCL(1); // 释放SCL，确保SCL为高电平
	OLED_W_SDA(0); // 在SCL高电平期间，拉低SDA，产生起始信号
	OLED_W_SCL(0); // 起始后把SCL也拉低，即为了占用总线，也为了方便总线时序的拼接
}

/**
 * 函    数：I2C终止
 * 参    数：无
 * 返 回 值：无
 */
void OLED_I2C_Stop(void)
{
	OLED_W_SDA(0); // 拉低SDA，确保SDA为低电平
	OLED_W_SCL(1); // 释放SCL，使SCL呈现高电平
	OLED_W_SDA(1); // 在SCL高电平期间，释放SDA，产生终止信号
}

/**
 * 函    数：I2C发送一个字节
 * 参    数：Byte 要发送的一个字节数据，范围：0x00~0xFF
 * 返 回 值：无
 */
void OLED_I2C_SendByte(uint8_t Byte)
{
	uint8_t i;

	/*循环8次，主机依次发送数据的每一位*/
	for (i = 0; i < 8; i++)
	{
		/*使用掩码的方式取出Byte的指定一位数据并写入到SDA线*/
		/*两个!的作用是，让所有非零的值变为1*/
		OLED_W_SDA(!!(Byte & (0x80 >> i)));
		OLED_W_SCL(1); // 释放SCL，从机在SCL高电平期间读取SDA
		OLED_W_SCL(0); // 拉低SCL，主机开始发送下一位数据
	}

	OLED_W_SCL(1); // 额外的一个时钟，不处理应答信号
	OLED_W_SCL(0);
}

/**
 * 函    数：OLED写命令
 * 参    数：Command 要写入的命令值，范围：0x00~0xFF
 * 返 回 值：无
 */
void OLED_WriteCommand(uint8_t Command)
{
	OLED_I2C_Start();			// I2C起始
	OLED_I2C_SendByte(0x78);	// 发送OLED的I2C从机地址
	OLED_I2C_SendByte(0x00);	// 控制字节，给0x00，表示即将写命令
	OLED_I2C_SendByte(Command); // 写入指定的命令
	OLED_I2C_Stop();			// I2C终止
}

/**
 * 函    数：OLED写数据
 * 参    数：Data 要写入数据的起始地址
 * 参    数：Count 要写入数据的数量
 * 返 回 值：无
 */
void OLED_WriteData(uint8_t *Data, uint8_t Count)
{
	uint8_t i;

	OLED_I2C_Start();		 // I2C起始
	OLED_I2C_SendByte(0x78); // 发送OLED的I2C从机地址
	OLED_I2C_SendByte(0x40); // 控制字节，给0x40，表示即将写数量
	/*循环Count次，进行连续的数据写入*/
	for (i = 0; i < Count; i++)
	{
		OLED_I2C_SendByte(Data[i]); // 依次发送Data的每一个数据
	}
	OLED_I2C_Stop(); // I2C终止
}

/*********************通信协议*/

/*硬件配置*********************/

/**
 * 函    数：OLED初始化
 * 参    数：无
 * 返 回 值：无
 * 说    明：使用前，需要调用此初始化函数
 */
void OLED_Init(void)
{
	OLED_GPIO_Init(); // 先调用底层的端口初始化

	/*写入一系列的命令，对OLED进行初始化配置*/
	OLED_WriteCommand(0xAE); // 设置显示开启/关闭，0xAE关闭，0xAF开启

	OLED_WriteCommand(0xD5); // 设置显示时钟分频比/振荡器频率
	OLED_WriteCommand(0x80); // 0x00~0xFF

	OLED_WriteCommand(0xA8); // 设置多路复用率
	OLED_WriteCommand(0x3F); // 0x0E~0x3F

	OLED_WriteCommand(0xD3); // 设置显示偏移
	OLED_WriteCommand(0x00); // 0x00~0x7F

	OLED_WriteCommand(0x40); // 设置显示开始行，0x40~0x7F

	OLED_WriteCommand(0xA1); // 设置左右方向，0xA1正常，0xA0左右反置

	OLED_WriteCommand(0xC8); // 设置上下方向，0xC8正常，0xC0上下反置

	OLED_WriteCommand(0xDA); // 设置COM引脚硬件配置
	OLED_WriteCommand(0x12);

	OLED_WriteCommand(0x81); // 设置对比度
	OLED_WriteCommand(0xCF); // 0x00~0xFF

	OLED_WriteCommand(0xD9); // 设置预充电周期
	OLED_WriteCommand(0xF1);

	OLED_WriteCommand(0xDB); // 设置VCOMH取消选择级别
	OLED_WriteCommand(0x30);

	OLED_WriteCommand(0xA4); // 设置整个显示打开/关闭

	OLED_WriteCommand(0xA6); // 设置正常/反色显示，0xA6正常，0xA7反色

	OLED_WriteCommand(0x8D); // 设置充电泵
	OLED_WriteCommand(0x14);

	OLED_WriteCommand(0xAF); // 开启显示

	OLED_Clear();  // 清空显存数组
	OLED_Update(); // 更新显示，清屏，防止初始化后未显示内容时花屏
}

/**
 * 函    数：OLED设置显示光标位置
 * 参    数：Page 指定光标所在的页，范围：0~7
 * 参    数：X 指定光标所在的X轴坐标，范围：0~127
 * 返 回 值：无
 * 说    明：OLED默认的Y轴，只能8个Bit为一组写入，即1页等于8个Y轴坐标
 */
void OLED_SetCursor(uint8_t Page, uint8_t X)
{
	/*如果使用此程序驱动1.3寸的OLED显示屏，则需要解除此注释*/
	/*因为1.3寸的OLED驱动芯片（SH1106）有132列*/
	/*屏幕的起始列接在了第2列，而不是第0列*/
	/*所以需要将X加2，才能正常显示*/
	//	X += 2;

	/*通过指令设置页地址和列地址*/
	OLED_WriteCommand(0xB0 | Page);				 // 设置页位置
	OLED_WriteCommand(0x10 | ((X & 0xF0) >> 4)); // 设置X位置高4位
	OLED_WriteCommand(0x00 | (X & 0x0F));		 // 设置X位置低4位
}

/*********************硬件配置*/

/*工具函数*********************/

/*工具函数仅供内部部分函数使用*/

/**
 * 函    数：次方函数
 * 参    数：X 底数
 * 参    数：Y 指数
 * 返 回 值：等于X的Y次方
 */
uint32_t OLED_Pow(uint32_t X, uint32_t Y)
{
	uint32_t Result = 1; // 结果默认为1
	while (Y--)			 // 累乘Y次
	{
		Result *= X; // 每次把X累乘到结果上
	}
	return Result;
}
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
